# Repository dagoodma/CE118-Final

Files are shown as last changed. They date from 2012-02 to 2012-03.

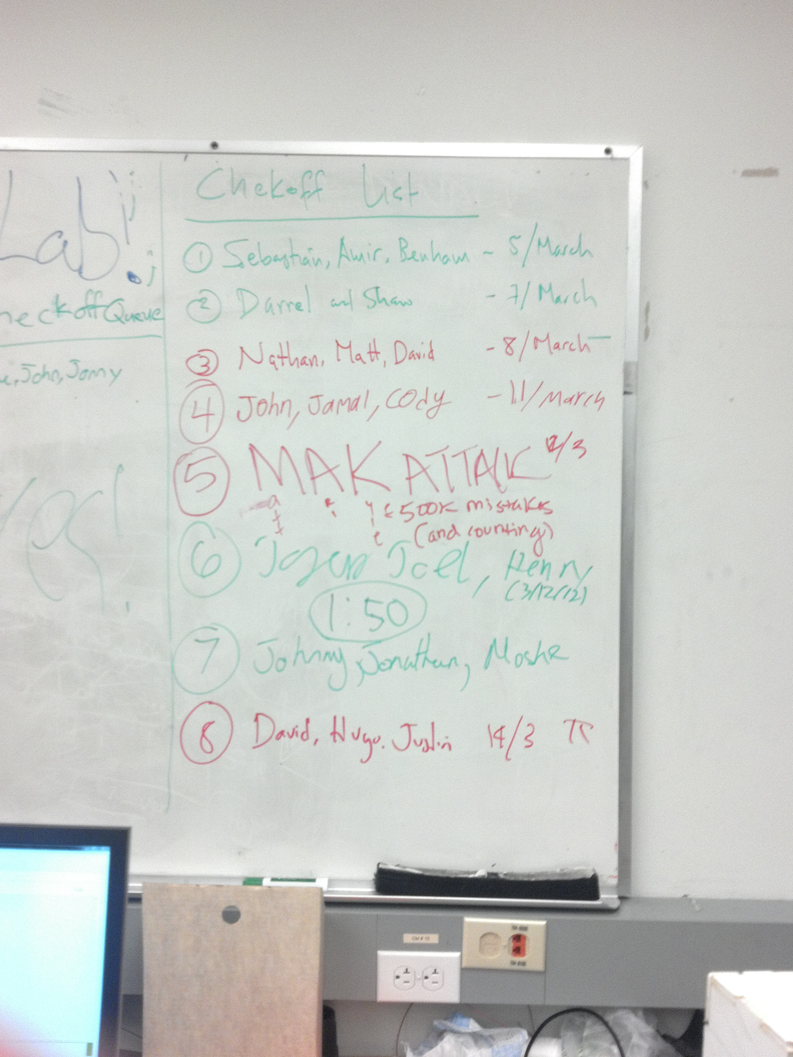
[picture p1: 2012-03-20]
Final Report/Pictures/Justin/checkoff board.jpg

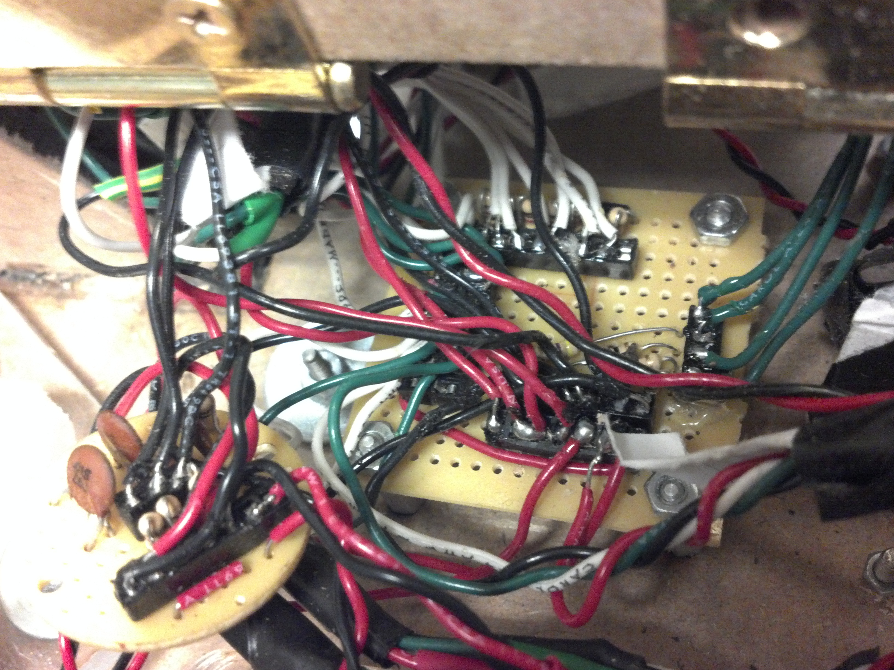
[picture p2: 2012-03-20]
Final Report/Pictures/Justin/bumper + tape board 2.jpg

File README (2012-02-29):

           . . . .... ......... ................            
              .  ...   .8DOOOOOOOD...............           
         .       . . .8OOOOOOOOOMNOOM,..........   M=7M     
  ....?  ............MOOOOOOOONNZOOOZN. ..  . ...~8  . ..  .
    N...,N .........8OOOOOOOOMM:.... O  .   .  .?, ONMM.    
  .,.,....=8........NOOOOOOID.  . .  : .     .OO.$  I. .    
  8...~:$ ... M7 ...OOOOD .M........ ......M:.: .   .M: .  .
...:..$.... .....,M.OOD..MMM : OMMM...,.M:......DM..........
....MMM,.. ,M8.....MMMMMMMMM..~MMMMM. 7 ....$N  ............
... ............7M8~$ DMMMMM.M MMMMM.. . N+.................
... .............. .M..OMMD MMZ ., M.:88 ...................
. .   ............N+ZO. ...,MMM ....MD......................
  .   .............N..++M...+  ...M M.......................
... ...............OOMZ.?........ ..  MN....................
... ............8Z7DO8O..+8::7:?+8.., ...,M~ ...............
......      :M?...8DOO8=..IMMMMM:..M .:M~....8M ....,O......
.....DMMNI .8 ..M,OOMO8O... ,=.8........ .M......=$....$....
....D7~?M7 ..=M...OODONNO.........8 ....... 7 ...DN , ,.....
...:... 7,.8:.....NOMOMOO=~......O............M...,~..O.....
...M..Z  .+ ......+OOONOM..MZNMM...............I ..::D .....
... ,..D Z    .  ..MONOOZ........................O ,O ......
....MM= 8.. .......$N.8OM.........................  ........
... ..     ...........8OZ...................................
......      ..........DM....................................
.......... .................................................

Future TODO:
----------------
* State machine and Code for tapesensors 
* Add pin names into schematics

Febuary 28, 2012
----------------
* Ready to print out of MDF
* Determine beacon switching with ULN2003A
    - update schematic
* Test gate servo
    - write code
* Prototype and test drive motor servo
* 

Febuary 21, 2012
----------------
* Prototyped geneva wheel: works.
* Started code.

/-----------------------------------------------------------\
--------------- How to use git -------------------
##Checkout from Github:
    git clone git@github.com:dagoodma/CE118-Lab

To commit code to the github first be sure your SSH public key is
generated in .ssh and added to your github account.

## See the changes files
    git status -s

## Add changed files
    git add -A

## Commit to local repository
    git commit -a -m "Your message"

## Commit to github (be sure to see http://help.github.com/create-a-repo/)
    git push -u origin master

-------- How to configure ssh public key  ------------

Once you have a github account you must configure your public ssh key
for each computer you wish to use.

## Generate an ssh-rsa public key
    ssh-keygen

Next, copy the contents of id_rsa.pub and login to your github account.
Under account settings > SSH Keys click Add New SSH Key, paste, and 
done.

## Configure info
    
    git config --global user.name "Your Name"
    git config --global user.email your@email.com

--------------- Add a repository -------------------

Next steps:
  mkdir CE118-Lab3
  cd CE118-Lab3
  git init
  touch README
  git add README
  git commit -m 'first commit'
  git remote add origin git@github.com:dagoodma/CE118-Lab3.git
  git push -u origin master
      
Existing Git Repo?
  cd existing_git_repo
  git remote add origin git@github.com:dagoodma/CE118-Lab3.git
  git push -u origin master

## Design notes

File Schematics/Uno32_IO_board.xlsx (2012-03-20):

CMPE118 Uno32 I/O Board Connection Table:
PIC32 Pin # | Connector Pin # | chipKIT Pin # | PIC32 Signal | Protection Pin # | Notes
15 | J5-16 | 41 | PGC1/AN1/VREF-/CVREF-/CN3/RB1 | Battery Voltage | Inaccesible from I/O
14 | J7-01 | A00/14 | C2IN-/AN2/SS1/CN4/RB2 | PORTV-3 | RC Servo | ADC
13 | J7-02 | A06/20 | C2IN+/AN3/CN5/RB3 | PORTV-4 | Gate (RC Servo) | ADC |  | RC Servo
12 | J7-03 | A01/15 | C1IN-/AN4/CN6/RB4 | PORTV-5 | TAPE_LEFT | ADC |  | Perfboard
11 | J7-03 | A07/21 | C1IN+/AN5/CN7/RB5 | PORTV-6 | TAPE_CENTER | ADC |  | Perfboard
21 | J7-05 | A02/16 | U2CTS/C1OUT/AN8/RB8 | PORTV-7 | TAPE_RIGHT | ADC |  | Perfboard
22 | J7-06 | A08/22 | PMA7/C2OUT/AN9/RB9 | PORTV-8 | TAPE_BACK | ADC |  | Perfboard
24 | J7-08 | A09/23 | TDO/PMA12/AN11/RB11 | PORTW-3 | TAPE_ARMFRONT | ADC |  | Perfboard
23 | J7-07 | A03/17 | TMS/CVREFOUT/PMA13/AN10/RB10 | PORTW-4 | TAPE_ARMLEFT | ADC |  | Perfboard
28 | J7-10 | A10/24 | TDI/PMA10/AN13/RB13 | PORTW-5 | TAPE_ARMRIGHT | ADC |  | Perfboard
27 | J7-09 | A04/18 | TCK/PMA11/AN12/RB12 | PORTW-6 | IR Main (RC Servo) | ADC |  | IR
30 | J7-12 | A11/25 | PMALL/PMA0/AN15/OCFB/CN12/RB15 | PORTW-7 | IR Angle (RC Servo) | ADC |  | IR
29 | J7-11 | A05/19 | PMALH/PMA1/U2RTS/AN14/RB14 | PORTW-8 | RC Servo | ADC
32 | J5-14 | 40 | PMA8/U2TX/SCL2/CN18/RF5 | PORTX-03 | LED_BANK3_2, RC | I/O
16 | J5-15 | 42 | PGED1/PMA6/AN0/VREF+/CVREF+/CN2/RB0 | PORTX-04 | LED_BANK3_3, RC | I/O
4 | J5-11 | 13 | SCK2/PMA5/CN8/RG6 | PORTX-05 | LED_BANK3_0 | I/O
31 | J5-12 | 39 | PMA9/U2RX/SDA2/CN17/RF4 | PORTX-06 | LED_BANK3_1 | I/O
5 | J5-09 or J5-07 | 12 | SDI2/PMA5/CN8/RG7 | PORTX-07/9 | LED_BANK2_2*, DNU | I/O
35 | J5-10 | 38 | U1RTS/BCLK1/SCK1/INT0/RF6 | PORTX-08 | TAPE_LEDS2 (LED_BANK2_3) | I/O | J2-9 (D) | ULN
6 | J5-07 or J5-09 | 11 | SDO2/PMA3/CN10/RG8 | PORTX-09/7 | LED_BANK2_0*, DNU | I/O
55 | J5-08 | 37 | CN16/RD7 | PORTX-10 | LED_BANK2_1 | I/O
52 | J5-05 | 10 | PMWR/OC5/IC5/CN13/RD4 | PORTX-11 | PWM5 | I/O
54 | J5-06 | 36 | CN15/RD6 | PORTX-12 | LED_BANK1_3 | I/O
45 | J5-04 | 35 | IC4/PMCS1/PMA14/INT4/RD11 | PORTY-03 | LED_BANK1_2 | I/O
51 | J5-03 | 9 | OC4/RD3 | PORTY-04 | PWM4, LED_BANK1_1 | I/O
53 | J5-02 | 34 | PMRD/CN14/RD5 | PORTY-05 | LED_BANK1_0 | I/O
44 | J5-01 | 8 | IC3/PMCS2/PMA15/INT3/RD10 | PORTY-06 | RC Servo | I/O
3 | J6-16 | 33 | PMD7/RE7 | PORTY-07 | RC Servo | I/O
43 | J6-15 | 7 | IC2/U1CTS/INT2/RD9 | PORTY-08 | TAPE_LEDS1 | I/O | J2-11 (F) | ULN
2 | J6-14 | 32 | PMD6/RE6 | PORTY-09 | Hbridge Dir A | I/O | J1-11 | Hbridge
50 | J6-13 | 6 | OC3/RD2 | PORTY-10 | Hbridge Step A (PWM3) | I/O | J1-12 | Hbridge
1 | J6-12 | 31 | PMD5/RE5 | PORTY-11 | Hbrige Dir B | I/O | J1-7 | Hbridge
49 | J6-11 | 5 | OC2/RD1 | PORTY-12 | Hbridge Step B (PWM6) | I/O | J1-8 | Hbridge
64 | J6-10 | 30 | PMD4/RE4 | PORTZ-03 | BUMPER_BR | I/O |  | Perfboard2
59 | J6-09 | 4 | RF1 | PORTZ-04 | BUMPER_BL | I/O |  | Perfboard2
63 | J6-08 | 29 | PMD3/RE3 | PORTZ-05 | BUMPER_BF | I/O |  | Perfboard2
46 | J6-07 | 3 | OC1/RD0 | PORTZ-06 | PWM1 | I/O
62 | J6-06 | 28 | PMD2/RE2 | PORTZ-07 | TAPE_LED | I/O | J2-12 (G) | ULN
42 | J6-05 | 2 | IC1/RTCC/INT1/RD8 | PORTZ-08 | RC Servo | I/O
61 | J6-04 | 27 | PMD1/RE1 | PORTZ-09 | RC Servo | I/O
33 | J6-03 | 1 | U1TX/SDO1/RF3 | PORTZ-10 | DO NOT USE | I/O
60 | J6-02 | 26 | PMD0/RE0 | PORTZ-11 | TAPE_LEDS3 | I/O | J2-10 (E) | ULN
34 | J6-01 | 0 | U1RX/SDI1/RF2 | PORTZ-12 | DO NOT USE | I/O

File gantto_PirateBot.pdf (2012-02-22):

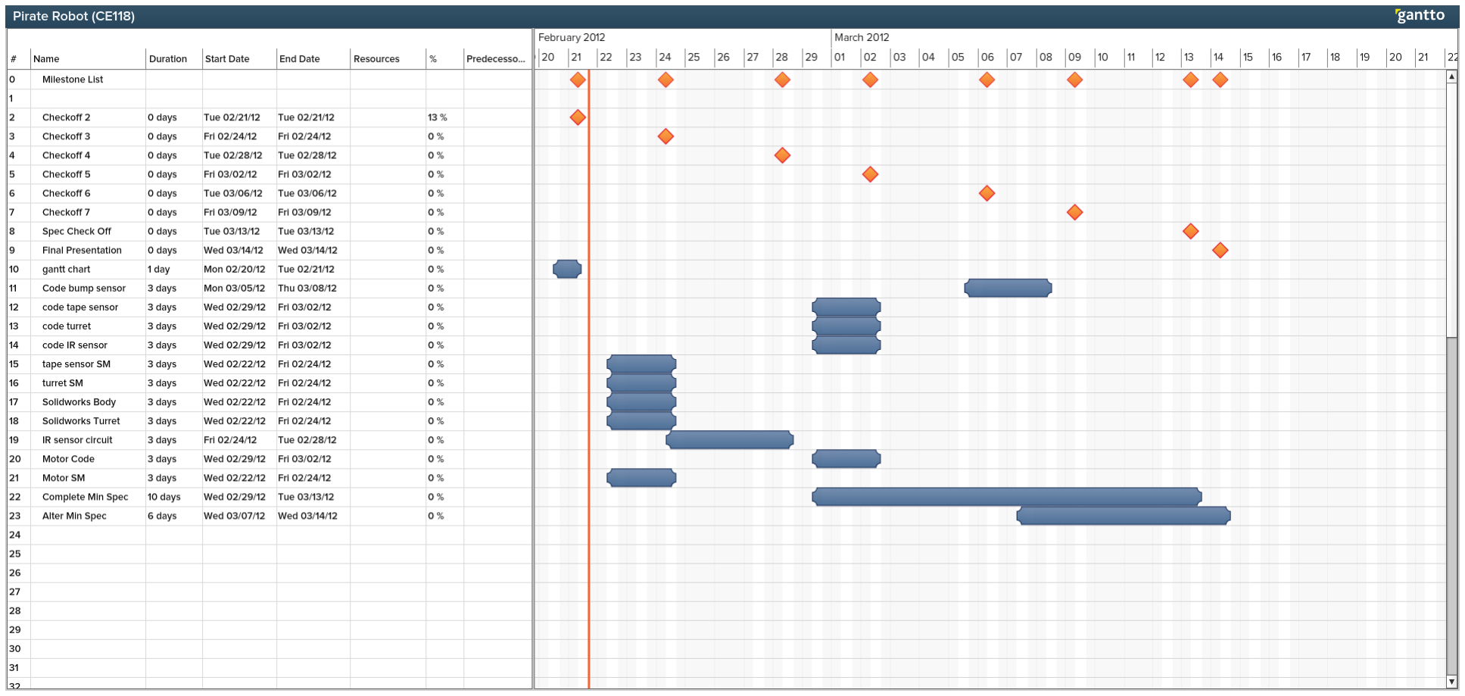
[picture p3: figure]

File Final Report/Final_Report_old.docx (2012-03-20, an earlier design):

Slugs of the Caribbean - Autonomous Robot
UCSC, CE118 Final Project

Introduction

The Slugs of the Caribbean project consisted of designing, constructing, programming, and testing an autonomous robot to meet the minimum specifications for the CE118 final project:

  - Navigate to the opposing island and back within two minutes
  - Hit the opponent with at least two ping pong balls
  - Stay within the field demarcated by two inch thick black tape
  - Detect and resolve collisions with an immovable object
  - The robot must be fully autonomous and cannot be controlled remotely

The project was assigned and completed within a five week period, and proved to be very challenging and time consuming. It taught us many new skills that drew from a variety of disciplines including: mechanical, electrical and computer engineering. Our goal was to develop the simplest robot possible, and later improve its capabilities as much as the remaining time allowed. Not everything worked out exactly as we had planned, but the end result successfully completed the minimum specification trial run with fifteen seconds to spare.

Designing and Planning

The three of us began the project by contributing five unique designs each, for a total of fifteen designs. The final design we chose to pursue was a combination of each of our best ones. However, we simplified the ping pong ball launcher into a box with a hinged gate that sprung open when released by an RC servo. Originally, we were designing a modular solution that would allow us to swap out the box for a rotating turret if we had the time to do so, which was not the case.

Both designs can be viewed below in figure 1.

<Minspec and turret schematics from first week>

A good portion of our time was spent in SolidWorks creating a comprehensive CAD model of our robot. Although we prototyped our design with foamcore, the final product was cut from MDF, and joined together using the tab and slot method. The CAD design of our robot is attached and can be seen in appendix A. A good amount of research and planning went into the actuators and sensors on our robot.

Drive motors

In order to make the robot mobile we purchased two 12 V, 140 RPM gearhead DC motors, which were screwed in and fixed to the body platform by motor mounts that we designed. These mounts consisted of a thin acrylic faceplate and MDF top and sidewalls. The motor shafts were attached to two wheels, which were made from thick acrylic, while the back and front of the robot was supported by skid plates created from ¼” thick bolts.

Collision sensors

Our durable collision sensors (bumpers) were made from thick acrylic plates that we cut and bent at ninety degree angles. The flat bumper plates were attached to the bent pieces with machine screws and nuts, and tension was maintained by short springs. Small push buttons were attached behind the bumpers to allow our robot to detect collisions.

Gate release

We used a servo motor as a gate release. When the servo was at the neutral position the gate would remain closed. Two springs were mounted behind the gate, and when the servo head was sent to the -45° position the gate was free to spring open. A motor mount was made for the servo out of MDF and attached just behind the gate.

Infrared Sensors

The infrared sensors that we designed and soldered in lab 2 proved to be robust enough to use on our final robot. We experimented with switching between two photodiodes on one circuit we elected to use two separate circuits detecting signals from two photodiodes oriented at an angle to allow for both long and short range detection. Each circuit was modified slightly to take an output from the peak detector allowing for software hysteresis. Both photodiodes were placed in MDF shielding to block light entering from the sides and give good directionality to our main beacon.

Tape Sensors

We used 7 of the TCRT5000 tape sensors provided in our lab kit for navigation of the course. Our arrangement allowed for high resolution coast following on the right side as well as detection of corners and the enemy base, with one sensor in the back to prevent reversing onto land. The ULN2003A board provided to us proved invaluable for simplification in driving our tape sensors, allowing for all 7 sensors to be switched easily using 3 ports on the PIC32. A perfboard with all our inputs and outputs as well as power and loading resistors for each LED/PD on the tape sensor had to be carefully soldered (twice) in order for our sensors to work properly.

Once a majority of the design work was completed we began by testing our design and creating prototypes of the actuator and sensor elements individually.

Prototyping and Modeling

To prototype our actuators and sensors we used foamcore instead of the more expensive MDF. Aside from prototyping the launcher and ‘geneva wheel’ loader for the turret design, which were never implemented, the first element we tested were our collision sensors.

us over the course of this project The microcontroller used by a PIC32MX320F128H donated by MicroChip.

…

The Tape Sensors

Our tape sensor implementation is fairly simple on its surface; however once we began to solder up all of the components its complexity became apparent. Each tape sensor has 4 leads, cathode and anode for the LED as well as collector and emitter for the photodiode. The LED anode and phototransistor cathode leads went into a board which provided 3.3V power from a TIP122 voltage regulator. Each LED needed a 150ohm loading resistor and was grounded with the ULN2003, capable of sinking current from two LEDs at each port. The photodiodes were placed in a sourcing configuration with a 1K resistor to ground with output was taken at the emitter using the ‘W’ analog port on the PIC32. The LEDs can be switched off and on by switching the ports on the ULN using the ‘Z’ ports and we then cascade through our analog inputs to take tape sensor readings.

As we soldered together our tape sensor board it quickly turned into a rats nest of wires leading into a small perfboard. 4 leads for each sensor * 7 sensors + 4 leads to the ULN meant we had 42 wires coming out of our perfboard, not to mention resistors and power regulation. This board was made even denser by the addition of bump sensor circuitry to the same perfboard. Despite the complexity our first assembled board worked reasonably well and we were able to use our sensors to design and implement our tape sensor code. Unfortunately with only a few days before min spec two of our tape sensors started to behave erratically, with no obvious software or hardware solution. After probing our tape sensor circuit for several hours we determined that there was no recourse but to resolder the whole board. Thankfully professor Elkaim was able to step in help us solder up the new board in record time.

The redone tape sensor board worked great, and all of our sensors gave readings close enough together that we did not have to deal with the additional complexity of separate thresholds for each sensor.

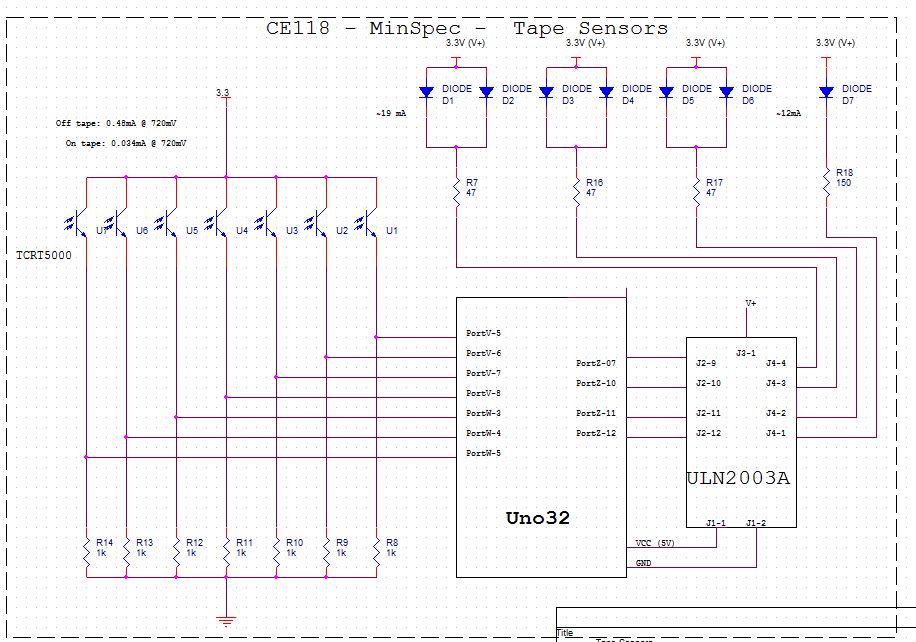
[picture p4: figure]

The software we used for the tape sensor made use of a simple state machine and a [synchronous?] sampling counter to ensure we had accurate readings at all times. Our state machine turned the leds on/off, took four readings, averaged them, repeated the process, and takes the difference of ‘ON’ and ‘OFF’ states to get a reading. High values correspond to being off tape, and low on tape. In practice we ended up taking only two samples during each state to speed up our sampling rate which in turn allowed us to navigate the course slightly faster. <insert state machine diagram?>

The Infrared Sensors

From very early on we wanted a two infrared sensor arrangement to allow for both long and short range detection of enemies, the idea being that we lock on with the main beacon and a second one placed at an angle notifies us when we are within range to dump / charge ahead over tape. Our original idea to save space on our bot and (in theory) reduce complexity was to switch two photodiodes on/off on the same circuit using a hex inverter. While we were able to implement a circuit that switched between two detectors on the same circuit we had nothing but trouble with interference between the two detectors. After working with the circuit trying to determine which capacitors weren’t discharging or where our initial voltage spikes were coming from we elected to cut our losses and place an additional sensing circuit on our board. While this detracted from the simplicity of our design it did not cost us any I/O ports and worked well with some minor alterations.

We first thought that we could get by with taking output from the comparator of the two circuits, saving us some software complexity, but quickly abandoned this idea in favor of a software comparator. The hardware comparator did not allow us much in the way of accuracy and our final navigation made use of a find max IR signal function which would not have been possible without taking output from our peak detectors. In order to get good resolution off our peak detector we had to alter it’s time constant for a faster discharge with a smaller resistor.

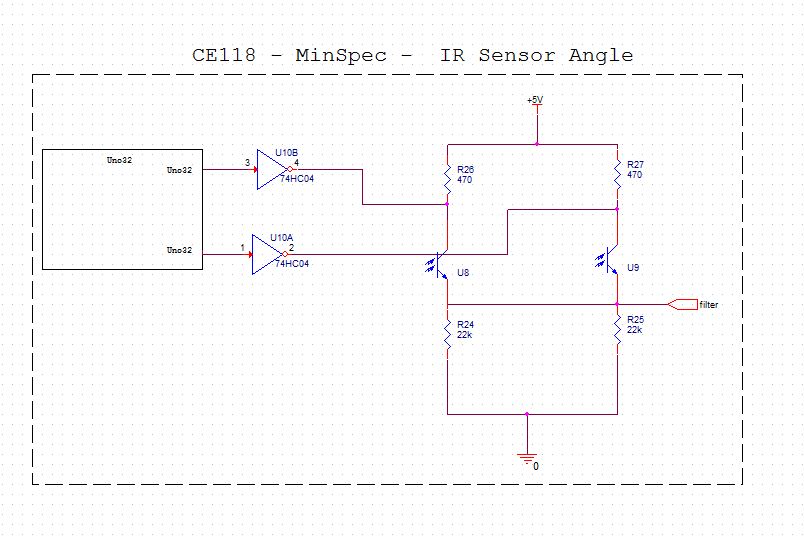
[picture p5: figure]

<switch schematic>

<David & Justin’s Schematics in appendix>

The Collision Sensors

In theory we wanted very robust bump sensors to allow us to ram into the other robots without sustaining any structural damage ourselves. In practice we ended up with some exquisitely designed bumpers that were perhaps somewhat overkill for our slow-moving robot.

Our durable collision sensors (bumpers) were made from thick acrylic plates that we cut and bent at ninety degree angles. The flat bumper plates were attached to the bent pieces with machine screws and nuts, and tension was maintained by short springs. Small push buttons were attached behind the bumpers to allow our robot to detect collisions.

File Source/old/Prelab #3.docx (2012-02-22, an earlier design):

Hugo A. Hernandez

David Goodman

Pre-Lab #3

0.1) Ports and pins to output to the motors in each part:

To drive the motor we will be using the following ports and pins on the: HBridge DRV8814, jumper stack J2 pins 1 and 2; DRV8811, jumper stack J2 pins 1 and 2; D53658, jumper stack J1 pin 1.

0.2) Initializations required:

Port Z pins 3,4,6,7,8 should be configured as outputs, and port V pin 5 as an input. The PORTS_SetPortDirection() function will be used to do this. Also, the A/D converter must be initialized with AD_Init(), the timer must be initialized with TIMERS_Init(), the RC Servo must be initialized with RC_Init(), the stepper motor will be initialized with Stepper_Init(), and the PWM must be initialized with PWM_Init();

0.3) ADC operating modes being used:

ADC_MODULE_ON Turn on ADC

ADC_FORMAT_INTG Output 16 bit unsigned int

ADC_CLK_AUTO Auto convert with internal counter

ADC_AUTO_SAMPLING_ON Auto sample

ADC_VREF_AVDD_AVSS Internal + and – voltage references configured

ADC_SCAN_ON ADC scan selection for CHO

ADC_BUF_16 16-bit word buffer

ADC_SAMPLE_TIME_31 31 Tad auto sample time

ADC_CONV_CLK_32Tcy A/D conversion clock select bit

ADC_CONV_CLK_PB A/D conversion clock from PB clock

0.4) Device connections:

Uno32 Connections

UNO Port-Pin | Device | Device Port-Pin | Comments
Z-03 | DRV8814 | J1-11 | Direction A
Z-04 | DRV8814 | J1-12 | Enable A
Z-07 | DRV8814 | J1-7 | Direction B
Z-08 | DRV8814 | J1-8 | Enable B
Z-03 | DRV8811 | J5-4 | Direction
Z-04 | DRV8811 | J5-5 | Enable
Z-06 | DRV8811 | J5-3 | PWM -> step
Z-06 | DS3658 | J2-9 | PWM -> Ch.A
V-05 | 50k pot | Middle Pin (Wiper) | (Input)

DRV8814 Connections

DRV8814 Port-Pin | Purpose | Comments
J1 | Inputs | See Uno32 Connections
J2-1 | Motor power
J2-2 | Motor ground
J3-1 | Power (8 – 30V)
J3-2 | High current ground
J6-open | Brake | Decay Mode
J6-closed | Coast | Decay Mode

DRV8811 Connections

DRV8811 Port-Pin | Purpose | Comment
J2-1 | Motor power
J2-2 | Motor ground
J5 | Inputs | See Uno32 Connections
J4|J3-00 | Full-Step | Coils Energized (2)
J4|J3-01 | Half-Step | Coils Energized (1-2)
J4|J3-01 | Quarter-Step | Coils Energized
J4|J3-11 | Eighth-Step | Coils Energized

DS3658 Connections

DS3658 Port-Pin | Purpose | Comment
J2 | Inputs | See Uno32 Connections
J1-1 | Motor power
J1-2 | Motor ground
J4-1 | +12V Supply
J4-2 | Ground
J3-open | Diodes unconnected | Kickback Diodes
J3-closed | Diodes to VCC | Kickback Diodes

0.5) Ribbon connector and the ports we will use are listed below:

Uno32 Port Z

1 | 3 | 5 | 7 | 9 | 11 | 13
| DirA/Step | En | DirB
| EnA/Dir | PWM-> Ch.A | EnB
2 | 4 | 6 | 8 | 10 | 12 | 14

DS3658

1 | 3 | 5 | 7 | 9 | 11 | 13
| | | | Ch. A
2 | 4 | 6 | 8 | 10 | 12 | 14
| | | DRV8814
1 | 3 | 5 | 7 | 9 | 11 | 13
| DirA | | DirB | | ?
| EnA | | EnB | | ?
2 | 4 | 6 | 8 | 10 | 12 | 14
| | | DRV8811
1 | 3 | 5 | 7 | 9 | 11 | 13
| Step | En
| Dir
2 | 4 | 6 | 8 | 10 | 12 | 14

0.6) PWM state diagram and an expected plot of its output at 10 kHz:

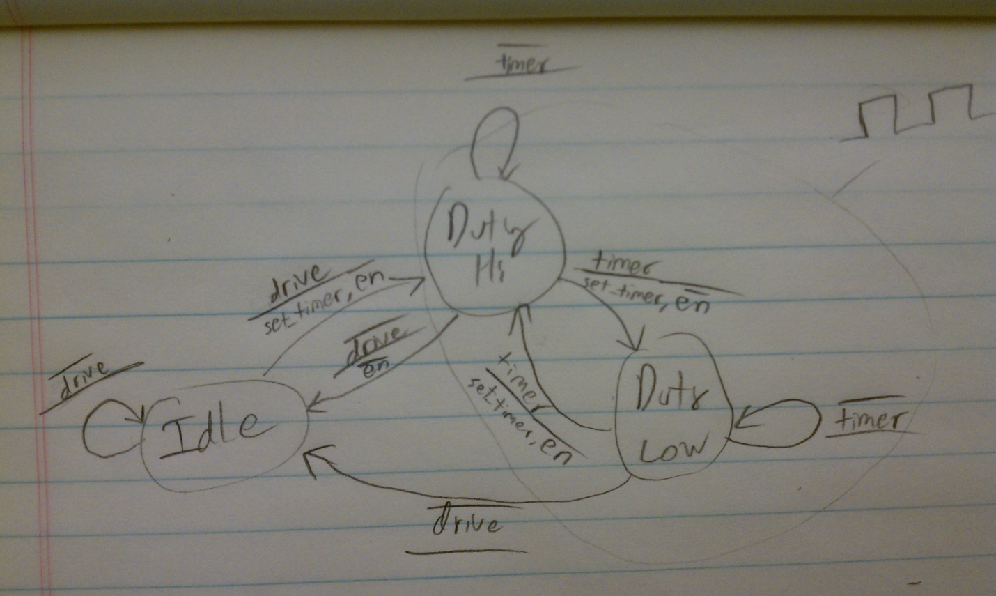
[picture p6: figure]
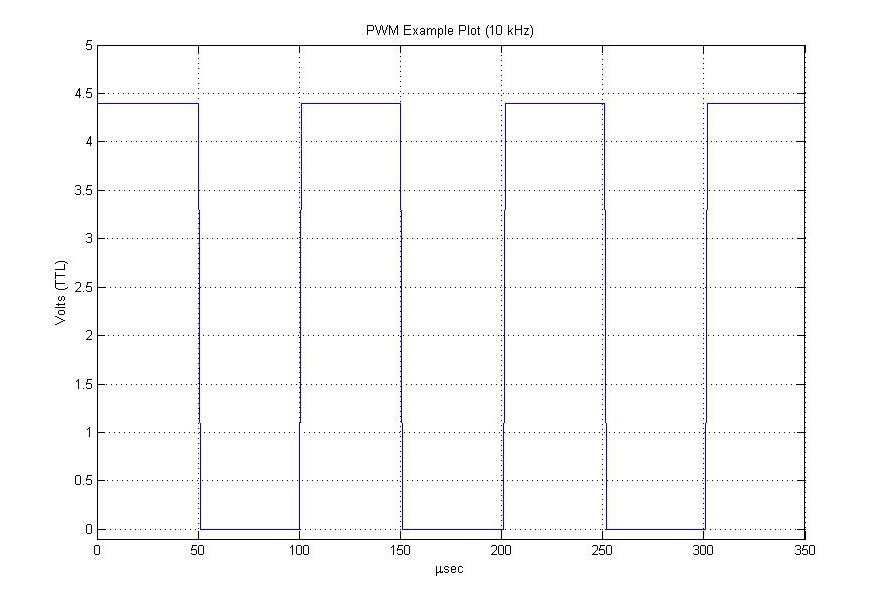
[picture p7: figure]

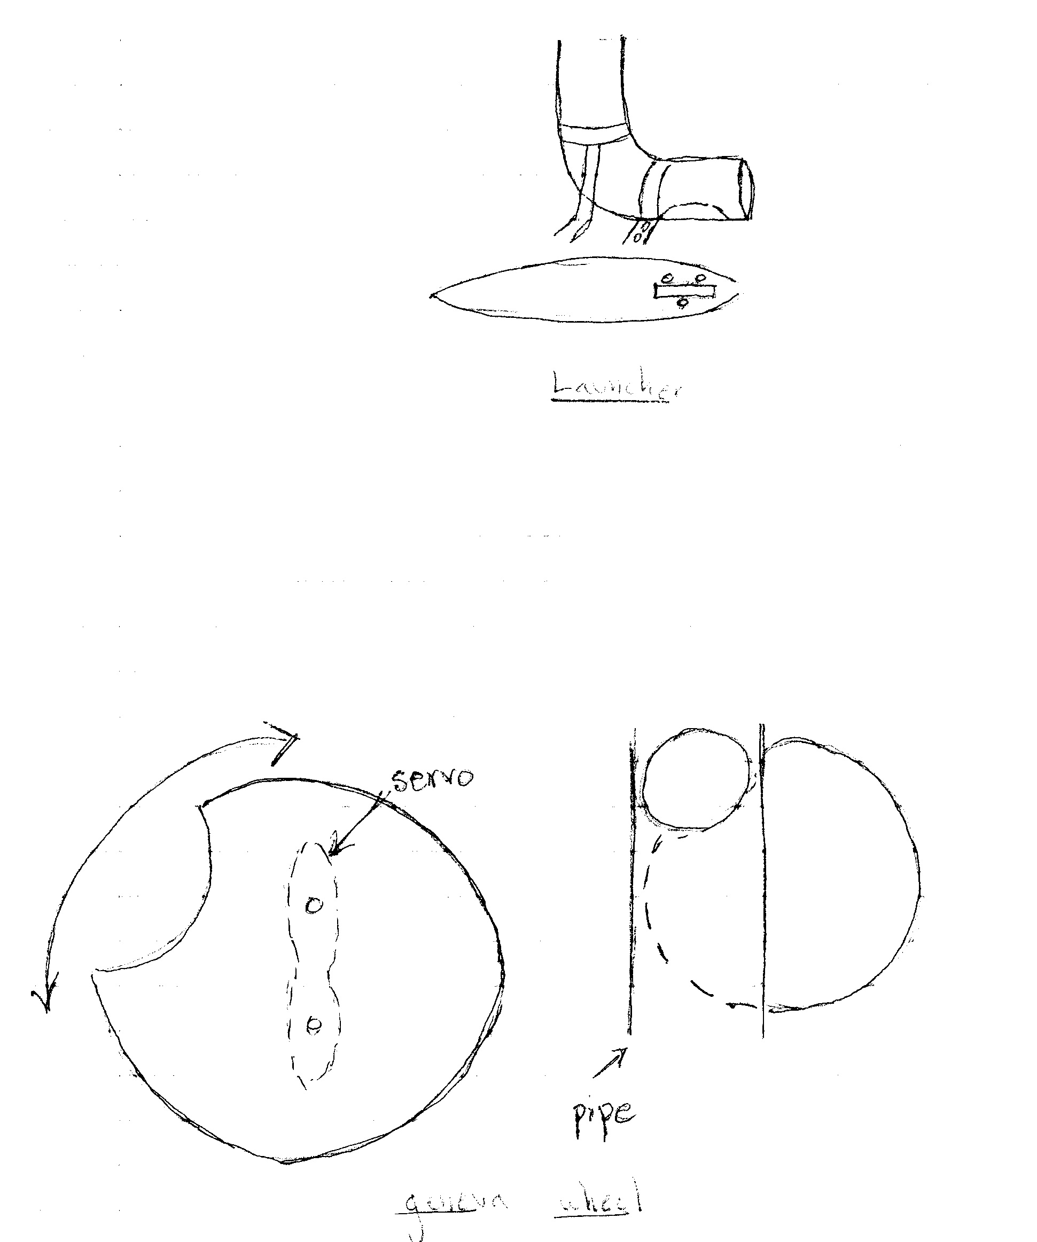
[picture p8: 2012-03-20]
Final Report/Pictures/Geneva Wheel.jpg

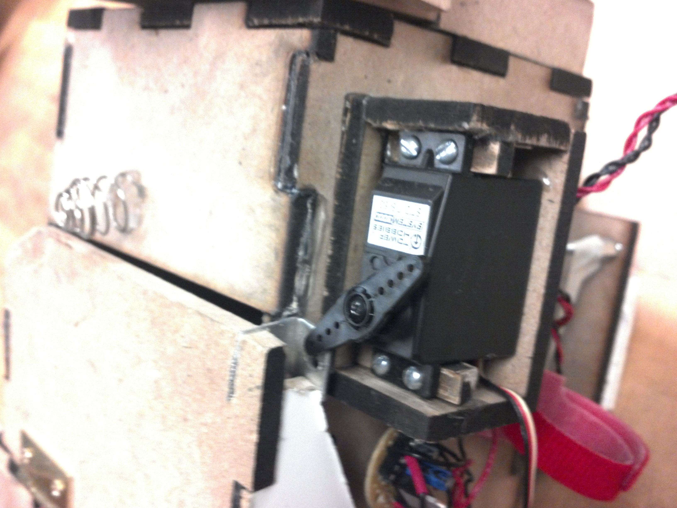
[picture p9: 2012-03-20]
Final Report/Pictures/Justin/servo gate.jpg

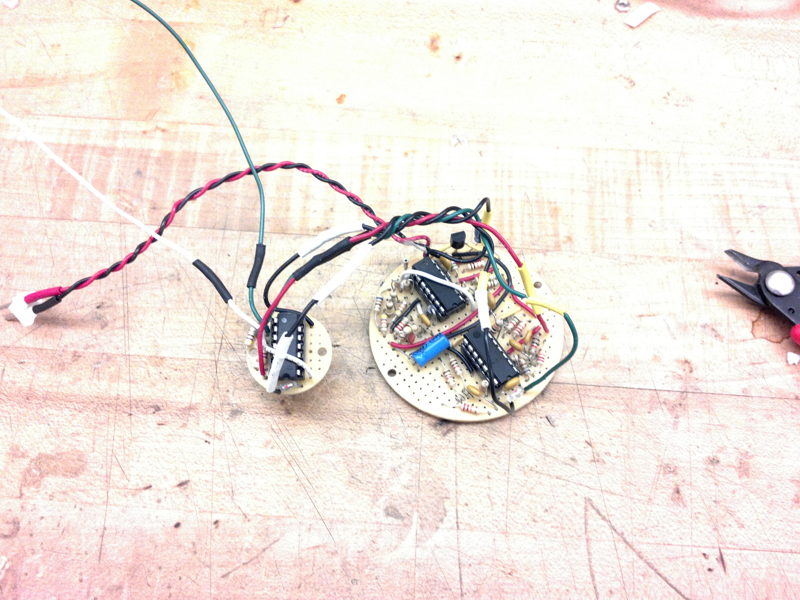
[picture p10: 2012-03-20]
Final Report/Pictures/Justin/IR + reg top.jpg

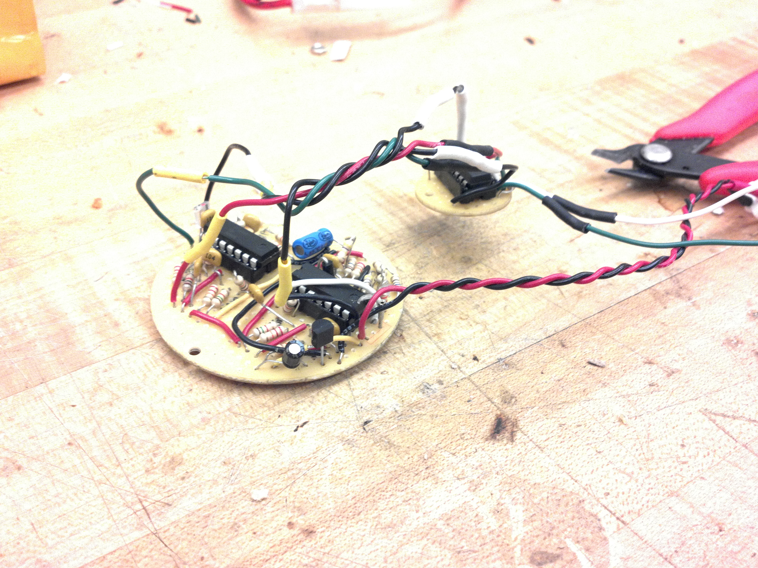
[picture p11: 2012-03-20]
Final Report/Pictures/Justin/IR + reg 2.jpg

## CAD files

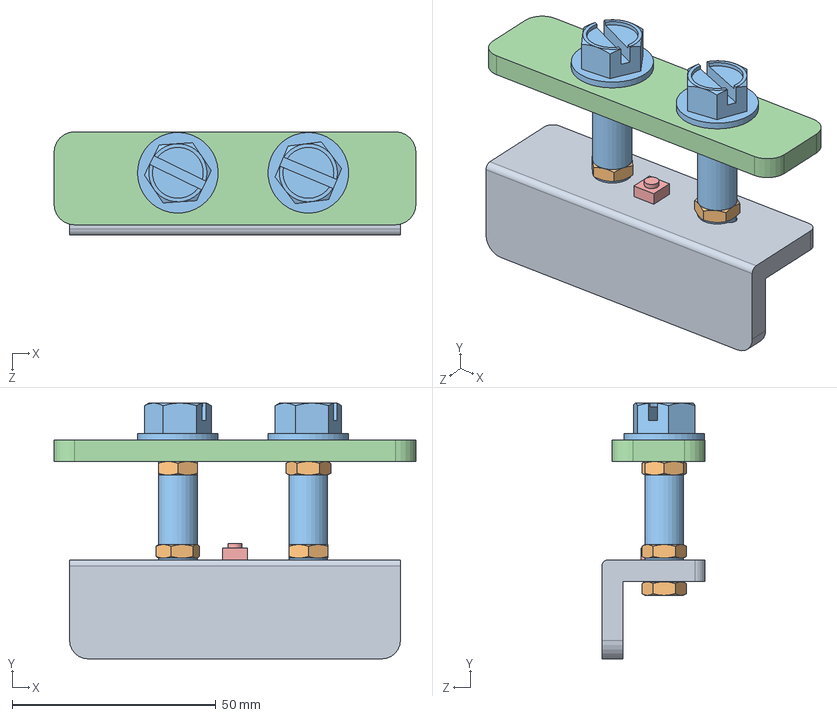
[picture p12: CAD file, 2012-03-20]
Solidworks/Bumper/Bumper_short.SLDASM
88.9 x 62.8 x 25.4 mm
bumperMount
machine screw nut hex_ai x 6
hex washer screw_ai x 2
bumperPlate_short
Button

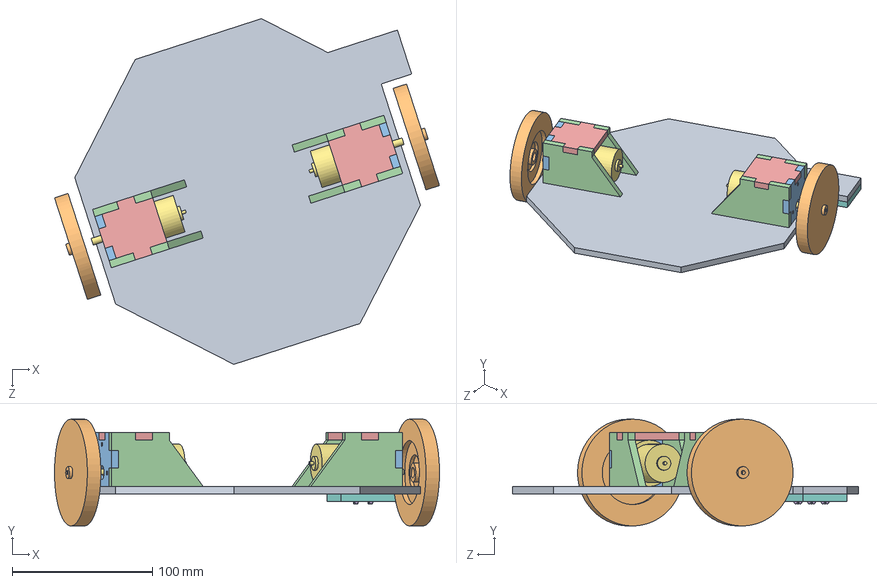
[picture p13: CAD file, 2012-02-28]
Solidworks/Platform.SLDASM
274.7 x 76.2 x 246.6 mm
base
Wheel x 2
motorMountFront x 2
motorMountSide x 4
motorMountTop x 2
tapeSensor_TCRT5000 x 3
12V65RPMGearheadMotor x 2
SideTapeSensorStand

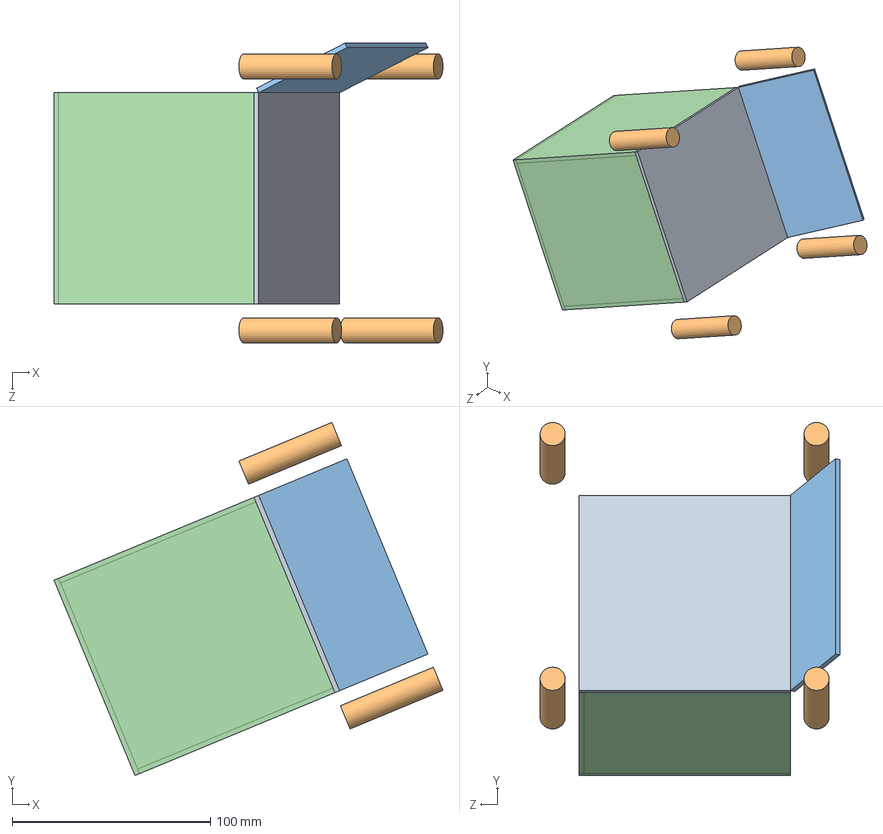
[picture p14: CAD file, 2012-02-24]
Solidworks/justin/PingPongBox.SLDASM
196.3 x 178.2 x 151.3 mm
BoxWall
BoxLeg x 4
HalfBoxWall x 2
boxWallWhole x 4

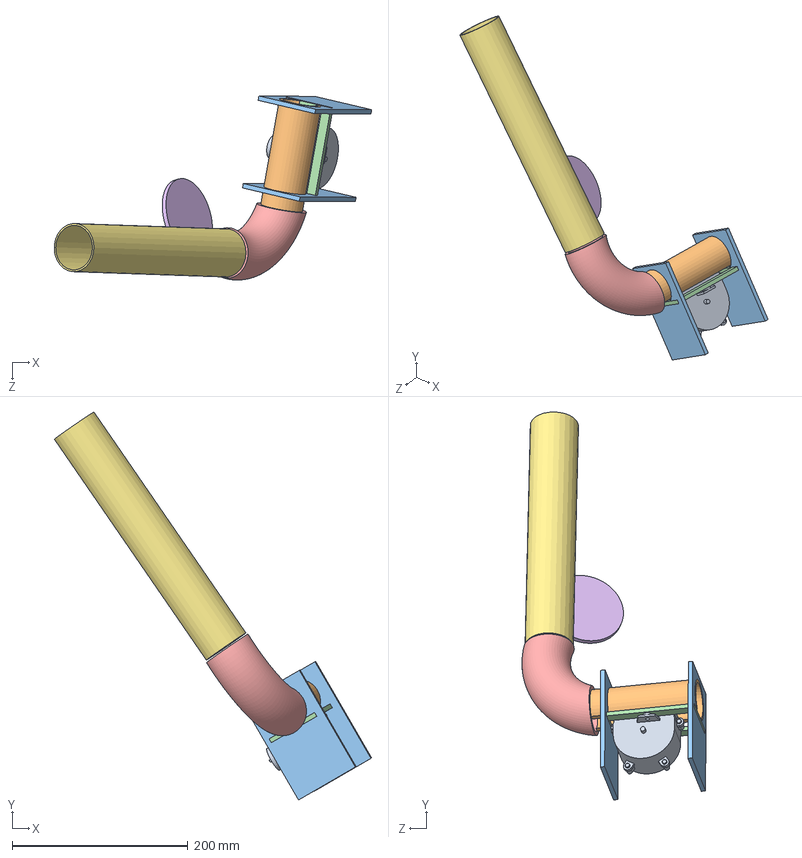
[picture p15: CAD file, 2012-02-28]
Solidworks/Launcher/Launcher with Mount.SLDASM
360.8 x 441.0 x 209.3 mm
ToyMotor
PVC_4.7in_cut
launch_side x 2
motor_mount
PVC_Elbow
genevaWheel
pvc
pingPongBall

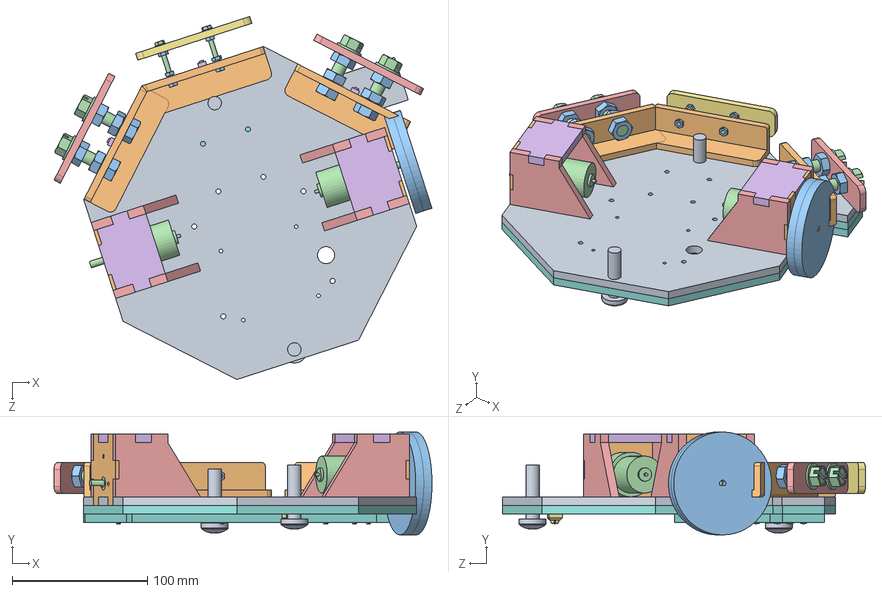
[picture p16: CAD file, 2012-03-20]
Solidworks/MinSpec/Platform.SLDASM
279.9 x 76.2 x 268.9 mm
base
mountFront2 x 2
wheelMDF x 2
12V65RPMGearheadMotor x 2
motorMountSide x 4
motorMountTop x 2
tapeSensor_TCRT5000 x 7
baseBottom
pan cross head_am x 2
bumperMount x 3
machine screw nut hex_ai x 18
hex washer screw_ai x 6
bumperPlate_short x 2
Button x 3
bumperPlate
tapePlatform

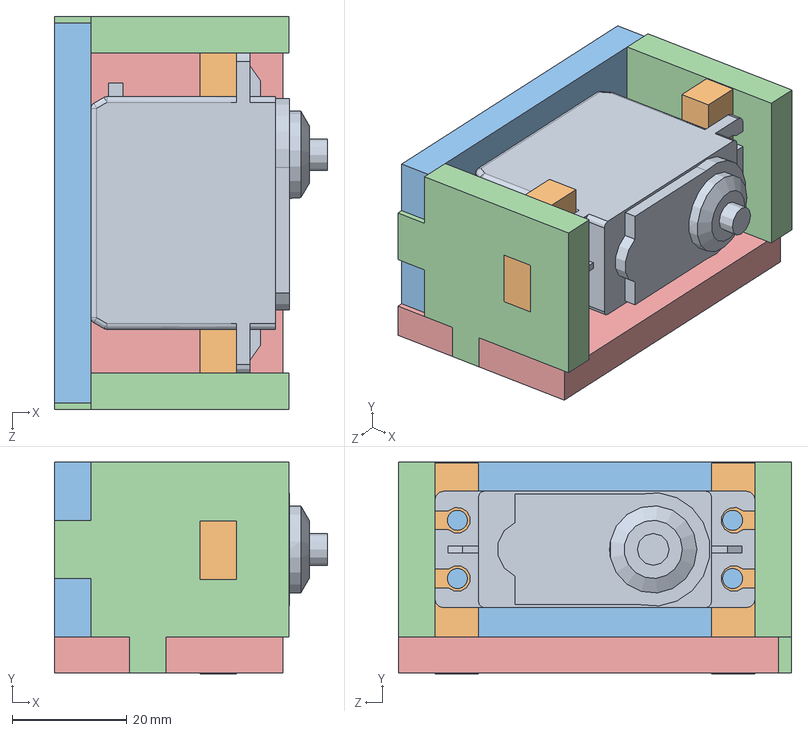
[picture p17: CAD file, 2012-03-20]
Solidworks/ServoBracket/ServoWithBracket.SLDASM
47.6 x 37.0 x 68.6 mm
servo
bracket_mount x 2
bracket_bottom
bracket_side2 x 2
bracket_back

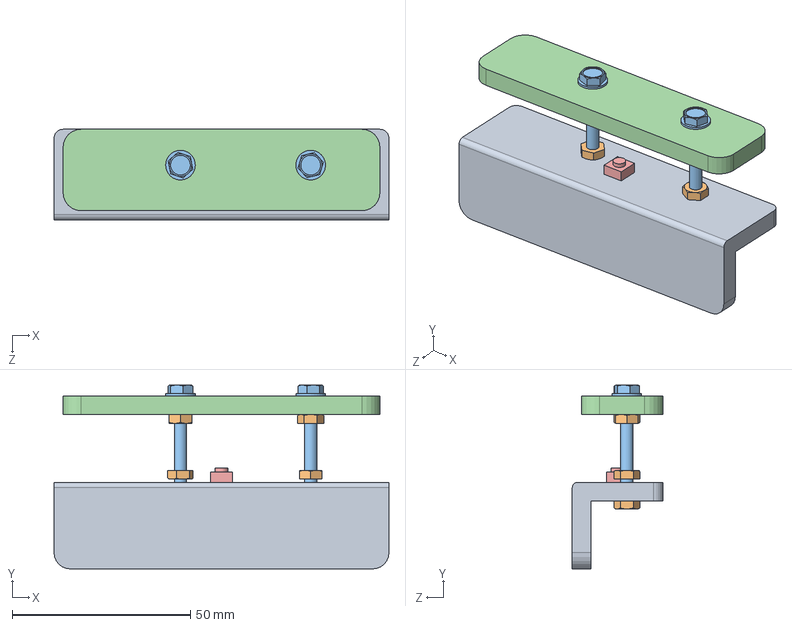
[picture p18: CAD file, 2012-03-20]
Solidworks/Bumper/Bumper.SLDASM
94.0 x 51.6 x 25.4 mm
bumperMount
machine screw nut hex_ai x 6
hex washer screw_ai x 2
bumperPlate
Button

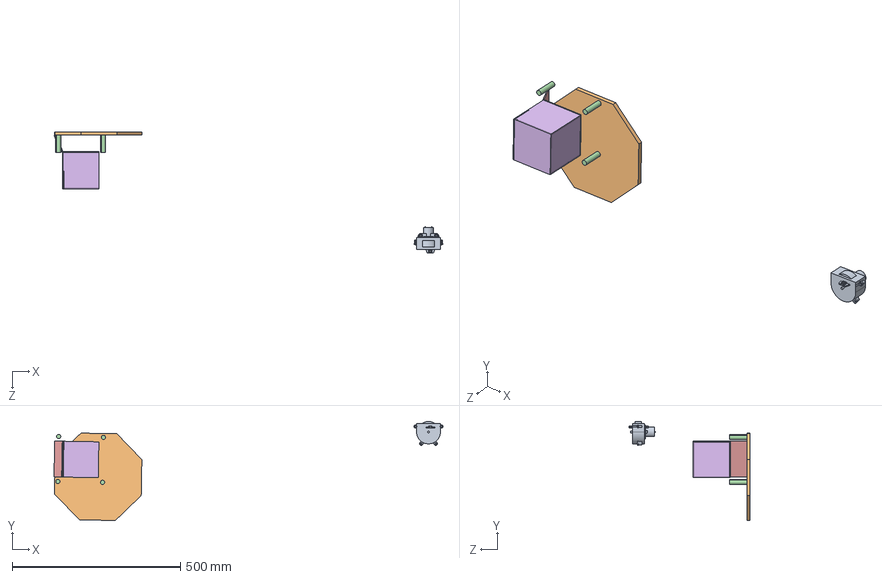
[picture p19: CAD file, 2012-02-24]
Solidworks/justin/FinalBot.SLDASM
1157.1 x 294.5 x 361.0 mm
ToyMotor
BotBody
BoxWall
BoxLeg x 4
HalfBoxWall x 2
boxWallWhole x 4

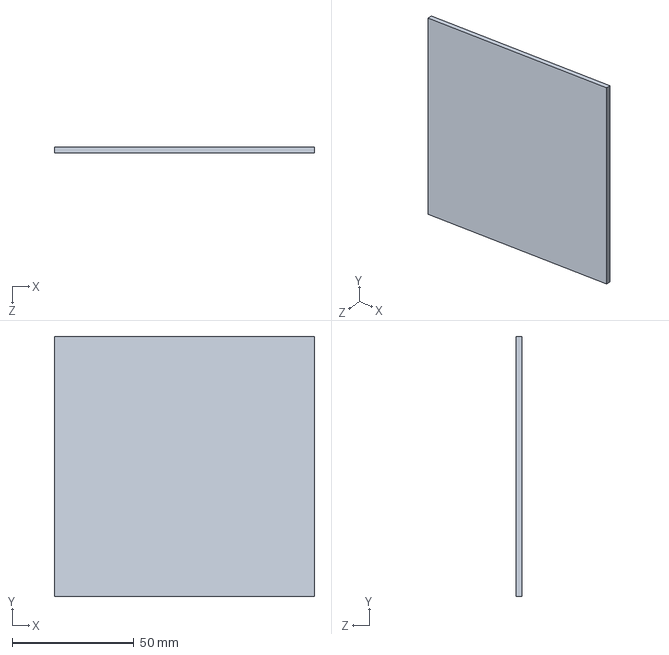
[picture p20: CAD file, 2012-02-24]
Solidworks/justin/boxWallWhole.SLDPRT
106.7 x 106.7 x 2.54 mm

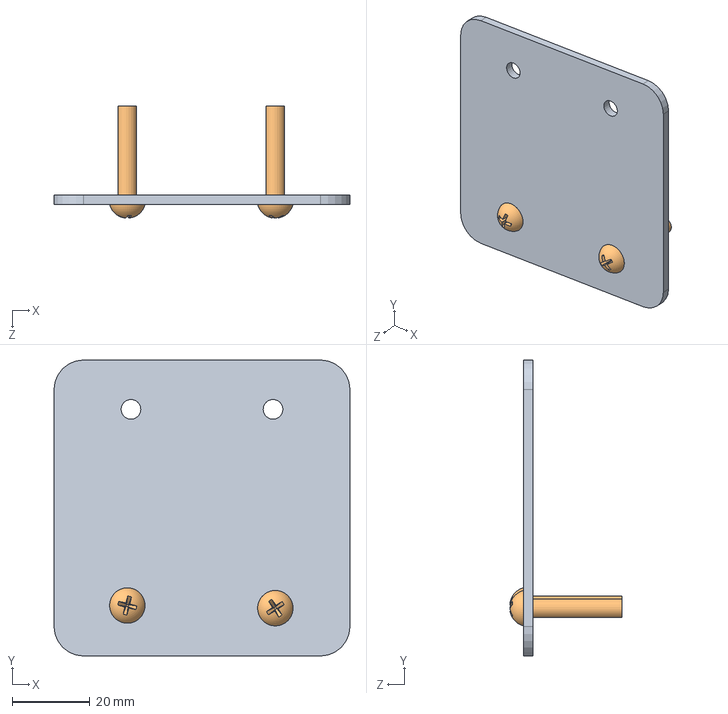
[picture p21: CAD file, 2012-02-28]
Solidworks/Bumper/lasercutter_bumer_base.SLDASM
76.2 x 76.2 x 28.8 mm
laser_cutter_acrylic_base
round head screw_ai x 2

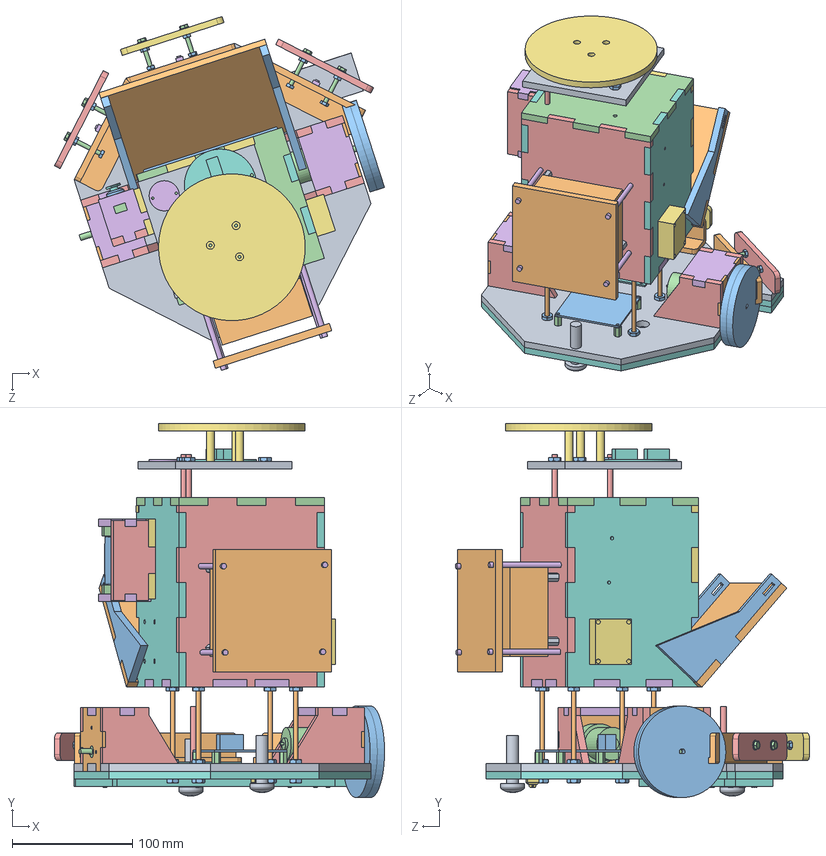
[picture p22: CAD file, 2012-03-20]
Solidworks/MinSpec/MinSpecRobot.SLDASM
274.3 x 310.9 x 294.1 mm
base
mountFront2 x 2
wheelMDF x 2
12V65RPMGearheadMotor x 2
motorMountSide x 4
motorMountTop x 2
tapeSensor_TCRT5000 x 8
baseBottom
pan cross head_am x 2
bumperMount x 3
machine screw nut hex_ai x 44
hex washer screw_ai x 6
bumperPlate_short x 2
Button x 3
bumperPlate
tapePlatform
pingPongBall
gate
gate_wall x 2
boxTop
boxBack
boxBottom
boxFront
boxSide x 2
standoffHex_uno32 x 4
uno32
hBridge_1_v2
standoffHex_hbridge x 4
Gate_Stop
beaconSensorSmall
beaconSensor
beaconPlatform
uno32ProtectorTop
servo
bracket_mount x 2
bracket_bottom
bracket_side2 x 2
bracket_back
servoHorn_2
truss head screw_ai x 4
boxBaseRod x 4
boxWedge_bottom
boxWedge_edge
beaconBoxRod x 2
ULN2003
bumperTapePerfBoard

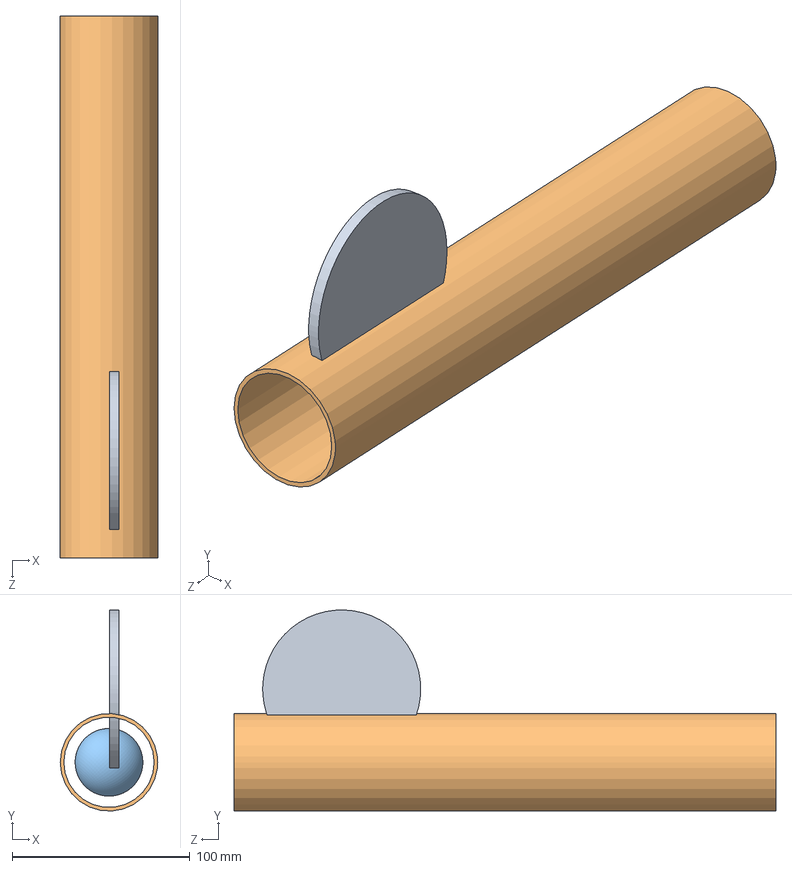
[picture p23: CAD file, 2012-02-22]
Solidworks/PitcherRelease.SLDASM
54.9 x 113.1 x 304.8 mm
genevaWheel
pvc
pingPongBall

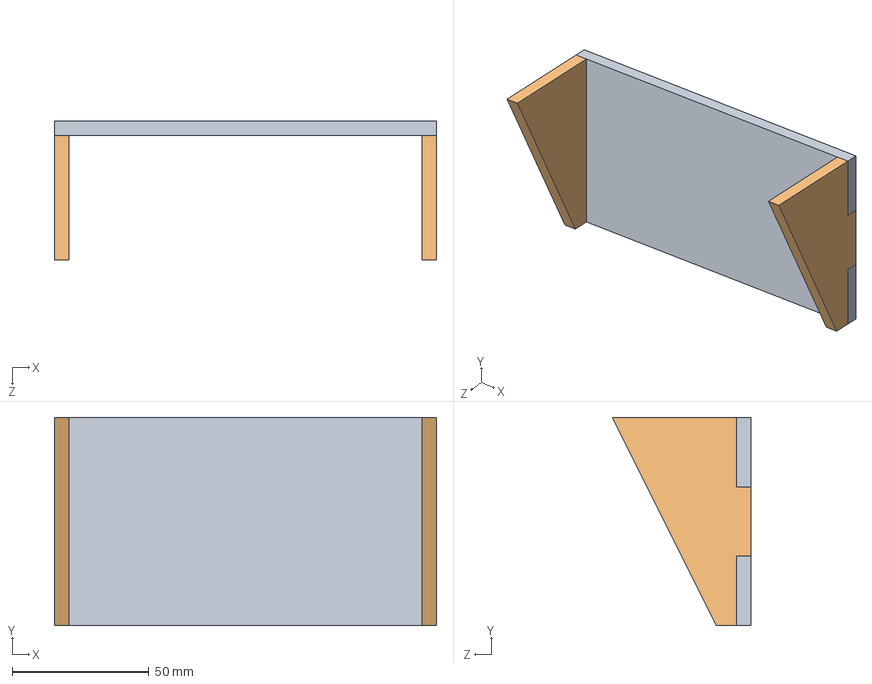
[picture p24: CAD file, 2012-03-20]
Solidworks/MinSpec/Gate.SLDASM
139.7 x 76.2 x 50.8 mm
gate
gate_wall x 2

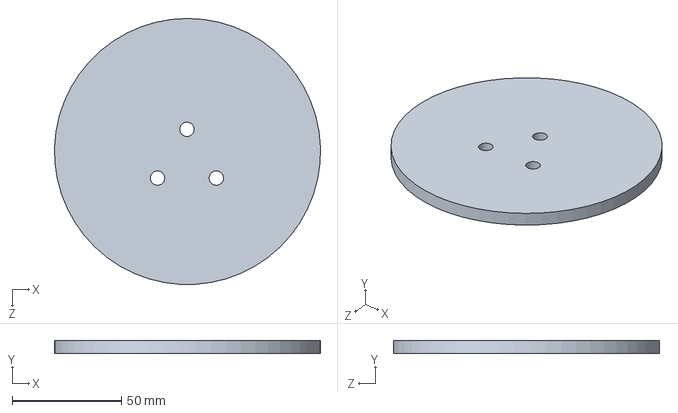
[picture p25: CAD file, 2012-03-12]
Solidworks/beacon.SLDPRT
121.9 x 6.10 x 121.9 mm

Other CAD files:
Solidworks/Bumper/lasercutter/Bumper_short.DXF
Solidworks/Drawings/tapePlatform.DXF
Solidworks/justin/boxFront.SLDPRT
Solidworks/Launcher/launcher_base.SLDPRT
Final Report/Solidworks Drawings/MinSpecRobot.SLDDRW
Final Report/Solidworks Drawings/base.SLDDRW
Solidworks/12V65RPMGearheadMotor.SLDPRT
Solidworks/Bumper/Button.SLDPRT
Solidworks/Bumper/bumperMount.SLDPRT
Solidworks/Bumper/bumperMount_LASER.SLDPRT
Solidworks/Bumper/bumperMount_short.SLDPRT
Solidworks/Bumper/bumperPlate.SLDPRT
Solidworks/Bumper/bumperPlate_short.SLDPRT
Solidworks/Bumper/bumperSpring_9657K730.SLDPRT
Solidworks/Bumper/laser_cutter_acrylic_base.SLDPRT
Solidworks/Bumper/lasercutter/Bumper.SLDDRW
Solidworks/Bumper/lasercutter/Bumper_back_laser.DXF
Solidworks/Bumper/lasercutter/Bumper_cdw_short.DXF
Solidworks/Bumper/lasercutter/Bumper_corel.DXF
Solidworks/Bumper/lasercutter/Bumper_large.DXF
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

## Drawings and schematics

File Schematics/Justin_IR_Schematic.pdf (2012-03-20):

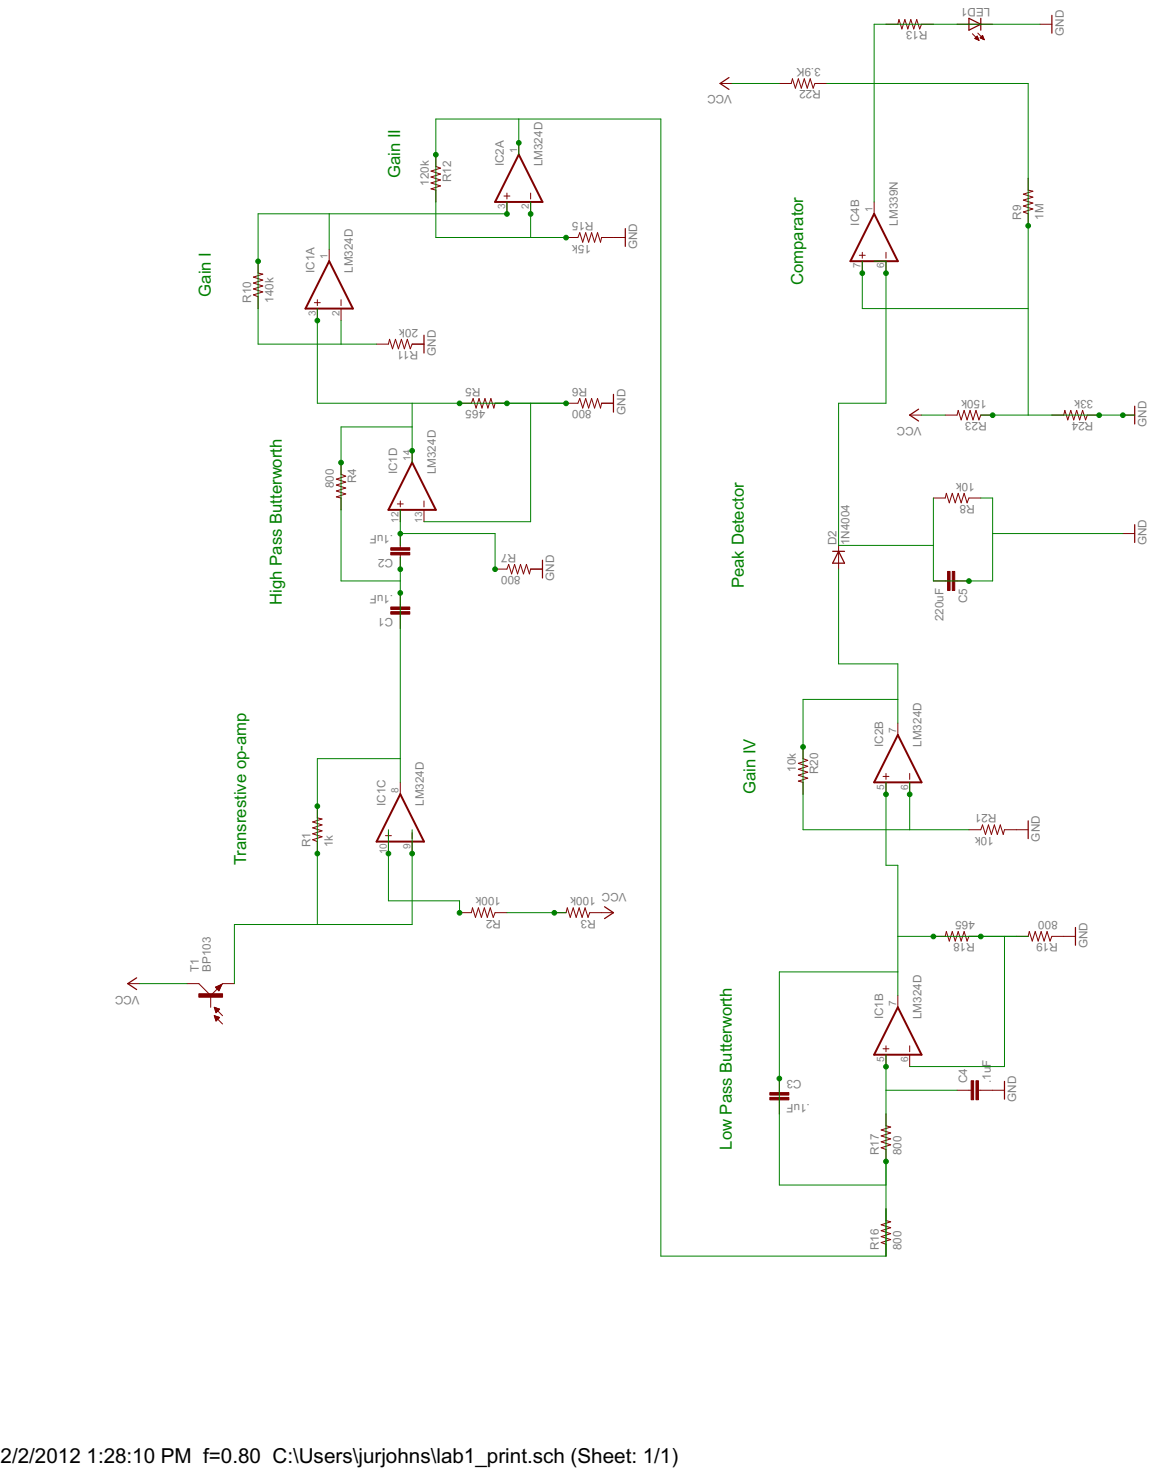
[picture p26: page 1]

High Pass Butterworth Gain I

GND GND

Low Pass Butterworth Gain IV

2/2/2012 1:28:10 PM f=0.80 C:\Users\jurjohns\lab1_print.sch (Sheet: 1/1)

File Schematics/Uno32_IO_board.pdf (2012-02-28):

# The CMPE 118 Uno32 I/O Board

Dept. of Computer Engineering, UCSC

## Background:

The ChipKit Uno32 module is a single-board computer produced by Digilent, Inc., which integrates a Microchip PIC3 microcontroller (PIC32MX320F128H), FTDI USB to Serial converter, voltage regulation, and 3.3V clamp diodes into a tidy little package. CMPE118 uses the Uno32 platform throughout the lab exercises and final project. The Uno32 is an Arduino compatible module, though we reflash the Arduino firmware to use a custom bootloader that allows us to program the PIC32 directly in C over the USB link.

However, the Uno32 wasn’t designed with CMPE118 in mind, so it isn’t exactly what we want, so we’ve designed and manufactured the Uno32 I/O board to get us closer to the ideal we are looking for.

The Uno32 I/O Board has several major functions:

1. Bring out all of the connections from the Uno32 to clearly defined and easily accessible ports with uniform connectors.
2. Provide a wide range of voltage input through an onboard switching regulator (6V to 30V).
3. Provide over-voltage and over-current protection circuitry on all port pins.
4. Provide LED banks for user visual outputs.
5. Provide both local and remote on/off power and reset switches
6. Provide reverse polarity protection
7. Provide fuse protected power distribution for additional circuits.

The data sheet for the ChipKit Uno32 can be found on the Digilentinc.com website at: http://www.digilentinc.com/Products/Detail.cfm?NavPath=2,892,893&Prod=CHIPKIT-UNO32

## Using the CMPE118 Uno32 I/O Board:

Using the CMPE118 Uno32 I/O Board should be straightforward. All the connections that will typically be made to the board are located around the edge of the board, and are clearly labeled and logically grouped. At the end of this document is a table which lists each pin on the PORT, along with its associated pins on the PIC32 microcontroller. All ports are clamped with diodes (TL7226) and series resistors to protect them from either overvoltage, undervoltage, or excessive currents.
Digital Input/Output Ports (PORT-X, PORT-Y, and PORT-Z):
Digital input and output ports are located on the three ports on the top of the board. They can be accessed either directly at the bit level through the #defines in the PORTS library, or as a word sized port through the functions contained within the library. Following the convention that microchip uses, the _TRIS registers are used to set output (0) or input (1) for each pin. The _LAT registers are used to write the output, and the _BIT registers to read from the port.

Port X, Y, and Z each have the outer two pins of the connectors grounded at the I/O board.

The pinout of PORT-X, PORT-Y, and PORT-Z are as follows:
PORT | Connection
Pin 1 | GND
Pin 2 | GND
Pin 3-12 | PORT-x 3-12
Pin 13 | GND
Pin 14 | GND

Digital and Analog Input/Output Ports (PORT-V and PORT-W):
Analog inputs (10bit ADC) are available on PORT-V and PORT-W, and can be set either as Analog or Digital I/O. The Analog pins can be accessed through the AD library, and the digital I/O can be accessed through the PORTS library.

Port V and W each have the outer pins connected to ground, and only have six pins each with the remaining pins connected to ground.

The pinout of PORT-V and PORT-W are as follows:
PORT | Connection
Pin 1 | GND
Pin 2 | GND
Pin 3-8 | PORT-w 3-8
Pin 9 | GND
Pin 10 | GND
Pin 11 | GND
Pin 12 | GND
Pin 13 | GND
Pin 14 | GND

Battery Voltage Monitoring:
The Uno32 I/O Board includes a precision 9:1 voltage divider connected to an ADC pin that is accessible through the AD library.

LED Banks:
The Uno32 I/O Board includes 12 LEDs organized into 3 banks of 4 LEDs each. They are connected to a subset of pins (see table at end) and are accessible through the LED library. The LED CONTROL jumper (JP7) connects the top of each bank of LEDs to the 3.3V rail through a set of current-limiting resistor banks. Leave them open if using them as normal I/O pins

Reset and Remote Reset (SW1 and JP3):
The Uno32 I/O Board includes a reset switch (SW1) as well as a remote reset jumper (JP3). The switch is a momentary contact switch which holds the PIC32 in reset while depressed. The remote switch works by shorting either of the outer pins to the center pin to reset the micro.
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

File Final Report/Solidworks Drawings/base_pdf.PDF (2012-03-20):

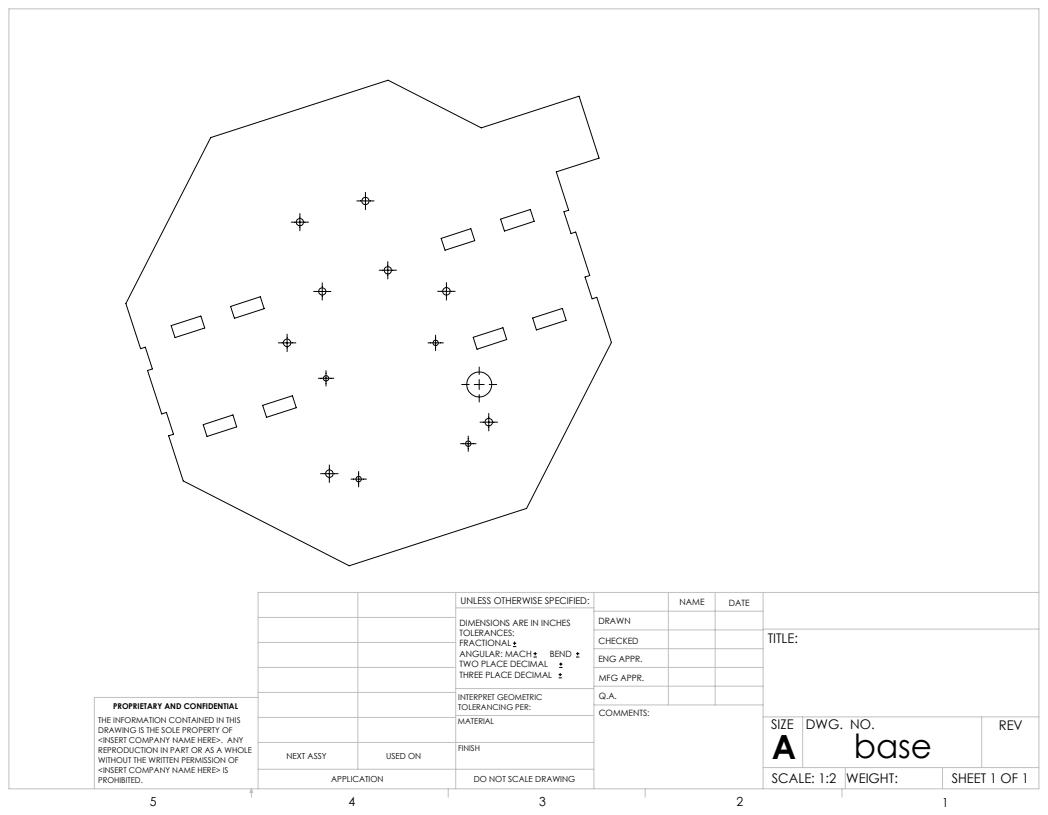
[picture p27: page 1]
SHEET 1 OF 1; SCALE: 1:2 WEIGHT:; DWG. NO.; REV; MFG APPR.; ENG APPR.; INTERPRET GEOMETRIC TOLERANCING PER:; ANGULAR: MACH; BEND; NEXT ASSY; USED ON

UNLESS OTHERWISE SPECIFIED:

DIMENSIONS ARE IN INCHES
TOLERANCES:
FRACTIONAL
TWO PLACE DECIMAL
THREE PLACE DECIMAL

PROPRIETARY AND CONFIDENTIAL
THE INFORMATION CONTAINED IN THIS
DRAWING IS THE SOLE PROPERTY OF
<INSERT COMPANY NAME HERE>. ANY
REPRODUCTION IN PART OR AS A WHOLE
WITHOUT THE WRITTEN PERMISSION OF
<INSERT COMPANY NAME HERE> IS
PROHIBITED.

DO NOT SCALE DRAWING

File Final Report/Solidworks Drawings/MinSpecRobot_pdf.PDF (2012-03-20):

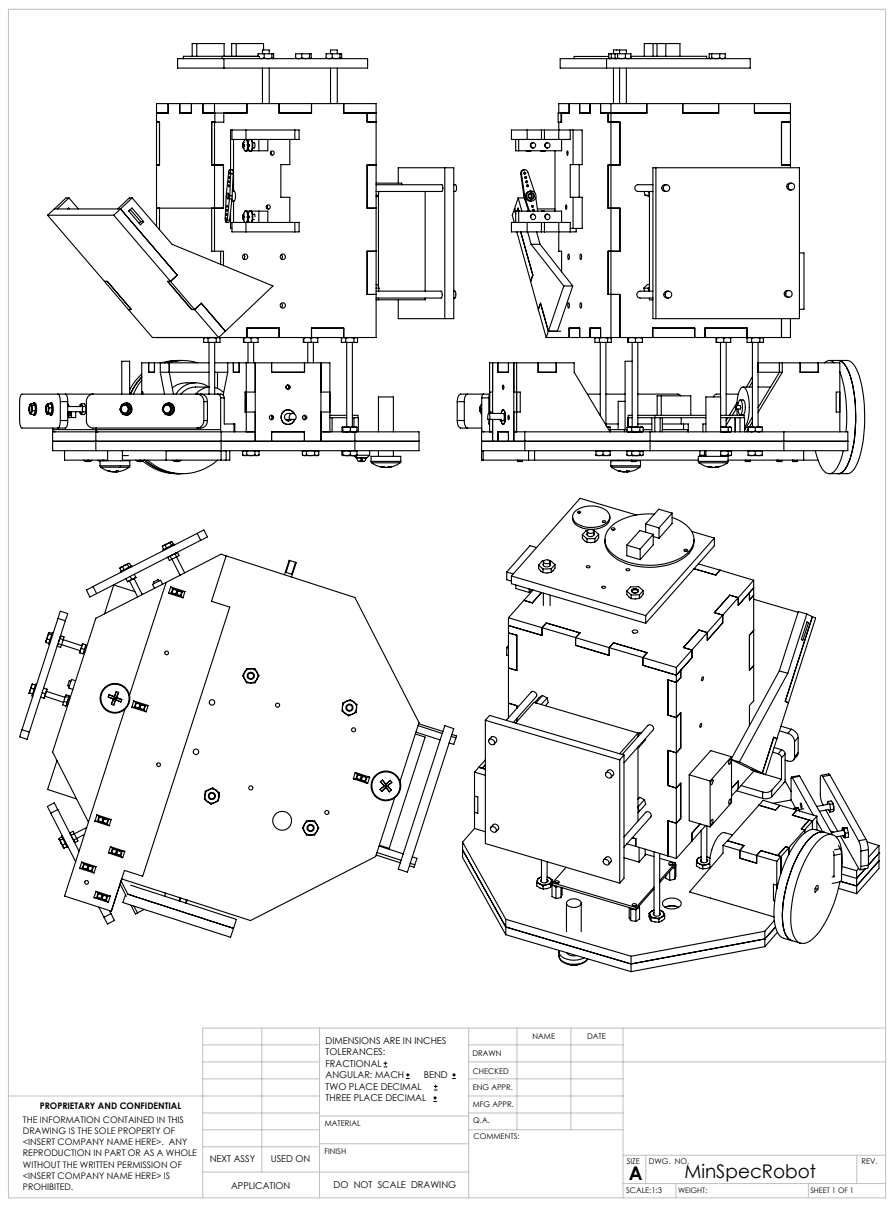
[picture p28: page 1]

TOLERANCES: FRACTIONAL ANGULAR: MACH BEND TWO PLACE DECIMAL THREE PLACE DECIMAL | | NAME | DATE DIMENSIONS ARE IN INCHES

DRAWN
CHECKED
ENG APPR.

PROPRIETARY AND CONFIDENTIAL THE INFORMATION CONTAINED IN THIS DRAWING IS THE SOLE PROPERTY OF <INSERT COMPANY NAME HERE>. ANY REPRODUCTION IN PART OR AS A WHOLE WITHOUT THE WRITTEN PERMISSION OF <INSERT COMPANY NAME HERE> IS PROHIBITED. | | | MFG APPR.

MATERIAL | Q.A.

NEXT ASSY | USED ON | FINISH

SIZE A | DWG. NO. MinSpecRobot | REV.

APPLICATION | | DO NOT SCALE DRAWING

SCALE:1:3 | WEIGHT: | SHEET 1 OF 1

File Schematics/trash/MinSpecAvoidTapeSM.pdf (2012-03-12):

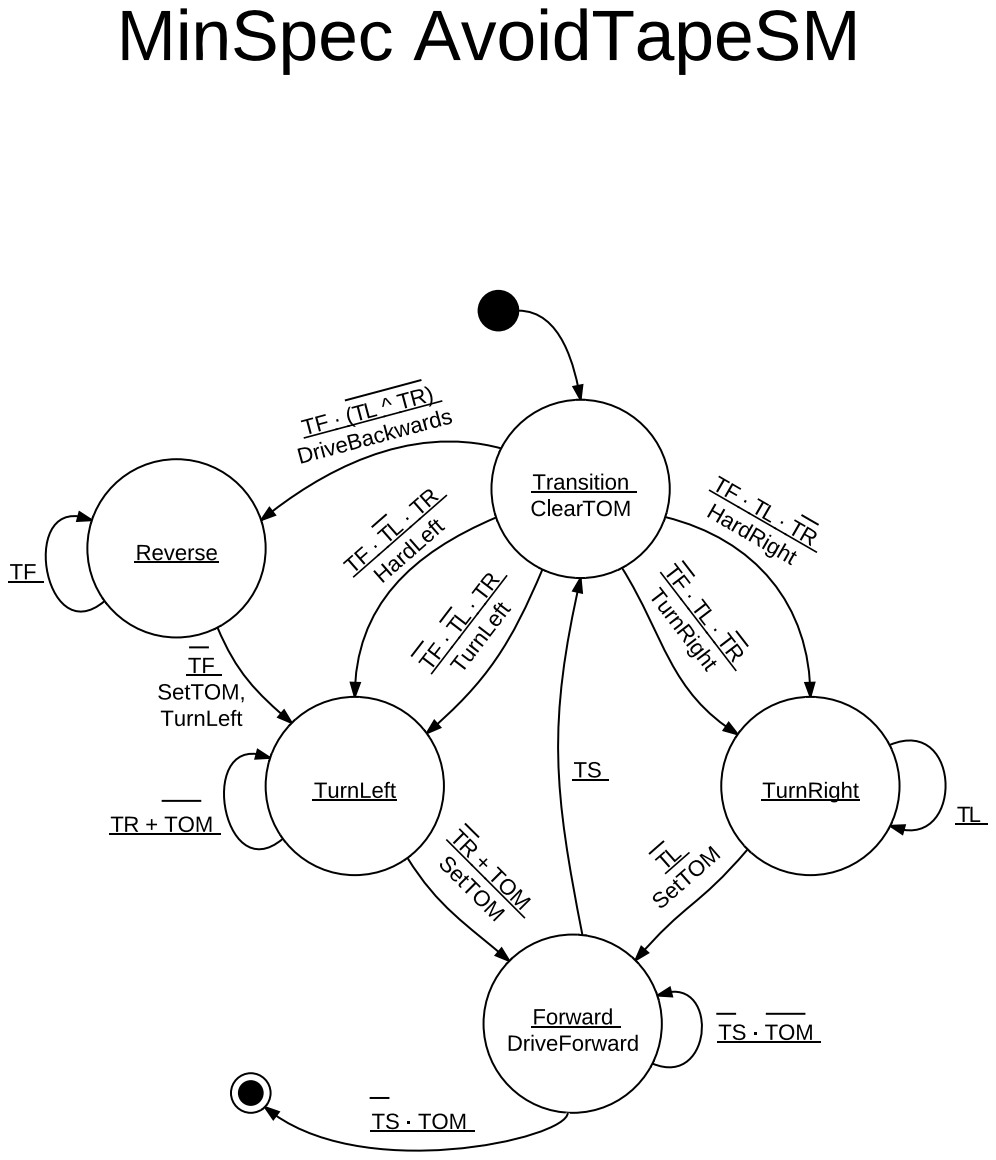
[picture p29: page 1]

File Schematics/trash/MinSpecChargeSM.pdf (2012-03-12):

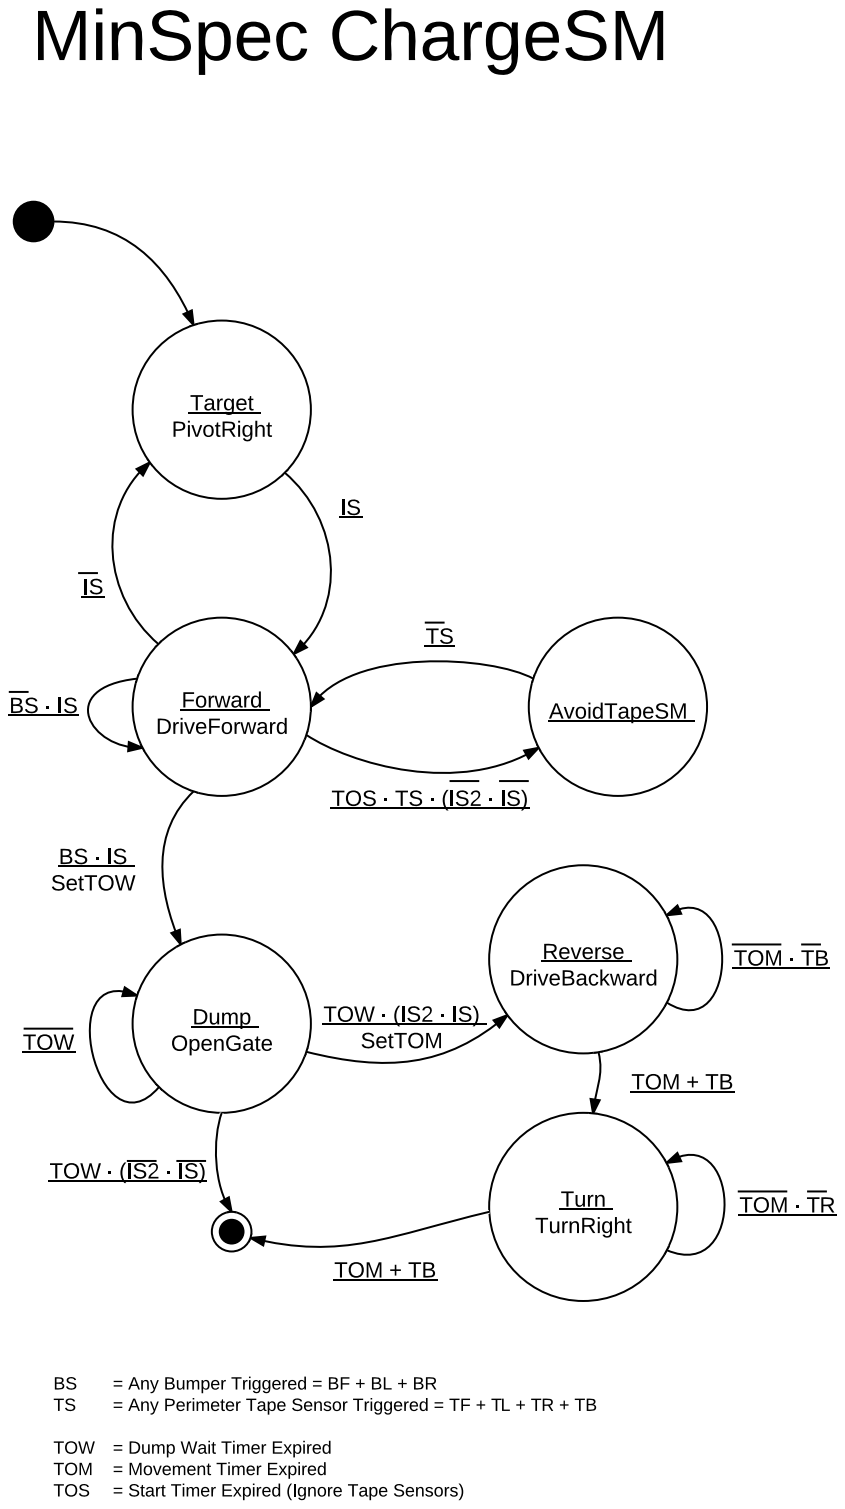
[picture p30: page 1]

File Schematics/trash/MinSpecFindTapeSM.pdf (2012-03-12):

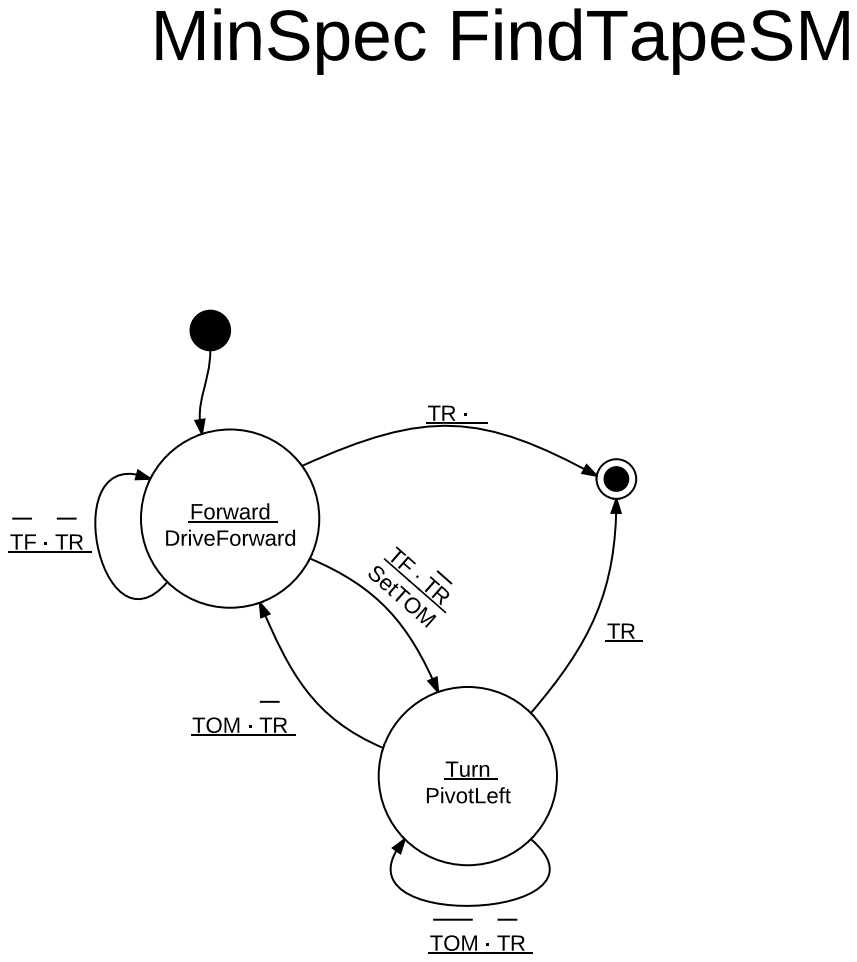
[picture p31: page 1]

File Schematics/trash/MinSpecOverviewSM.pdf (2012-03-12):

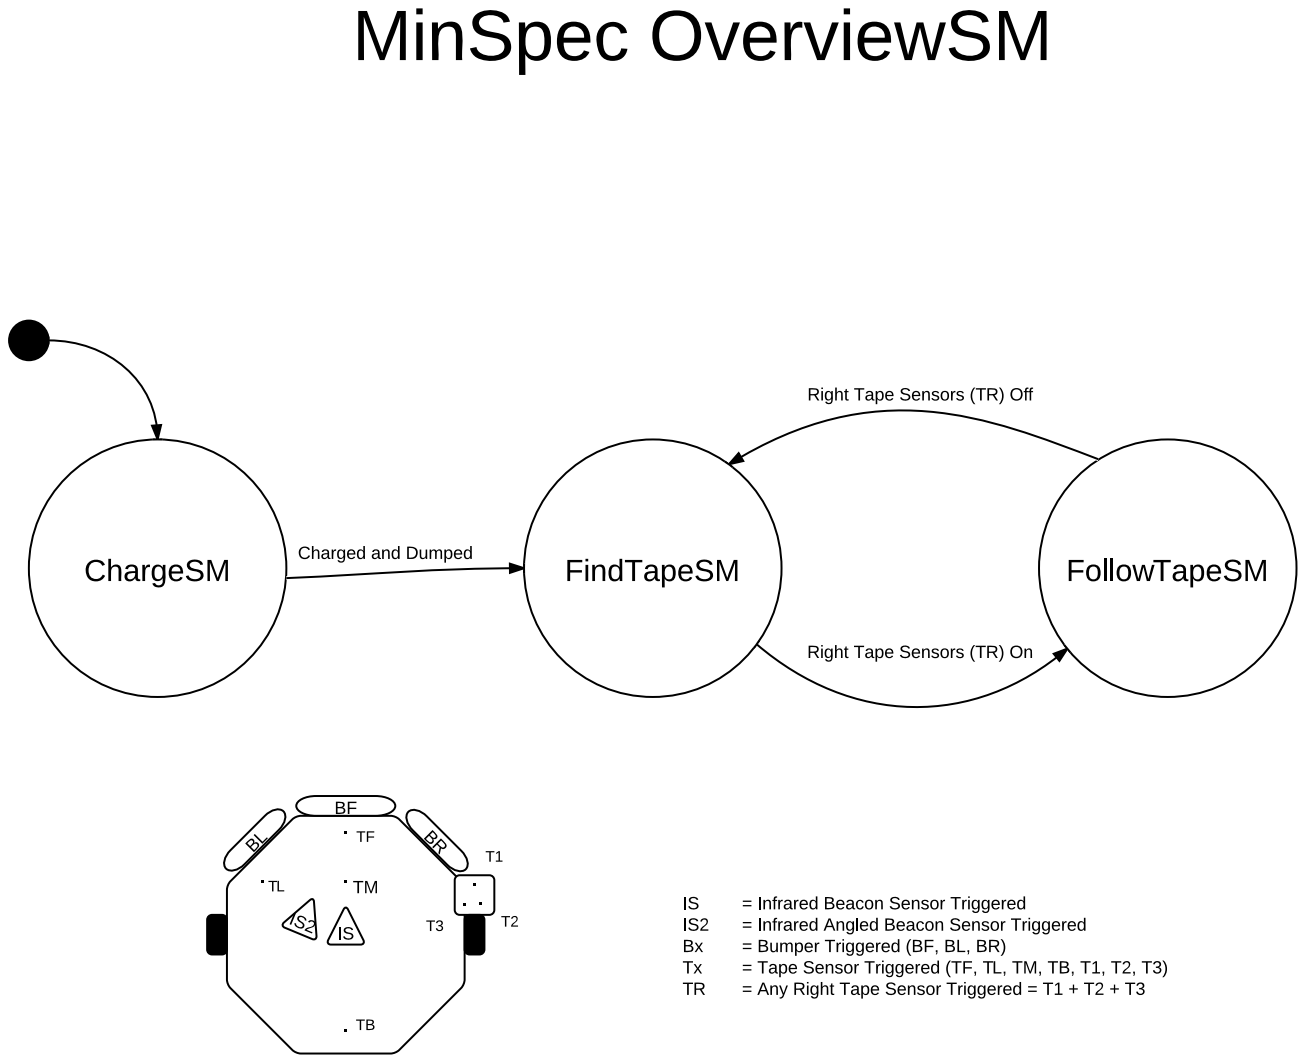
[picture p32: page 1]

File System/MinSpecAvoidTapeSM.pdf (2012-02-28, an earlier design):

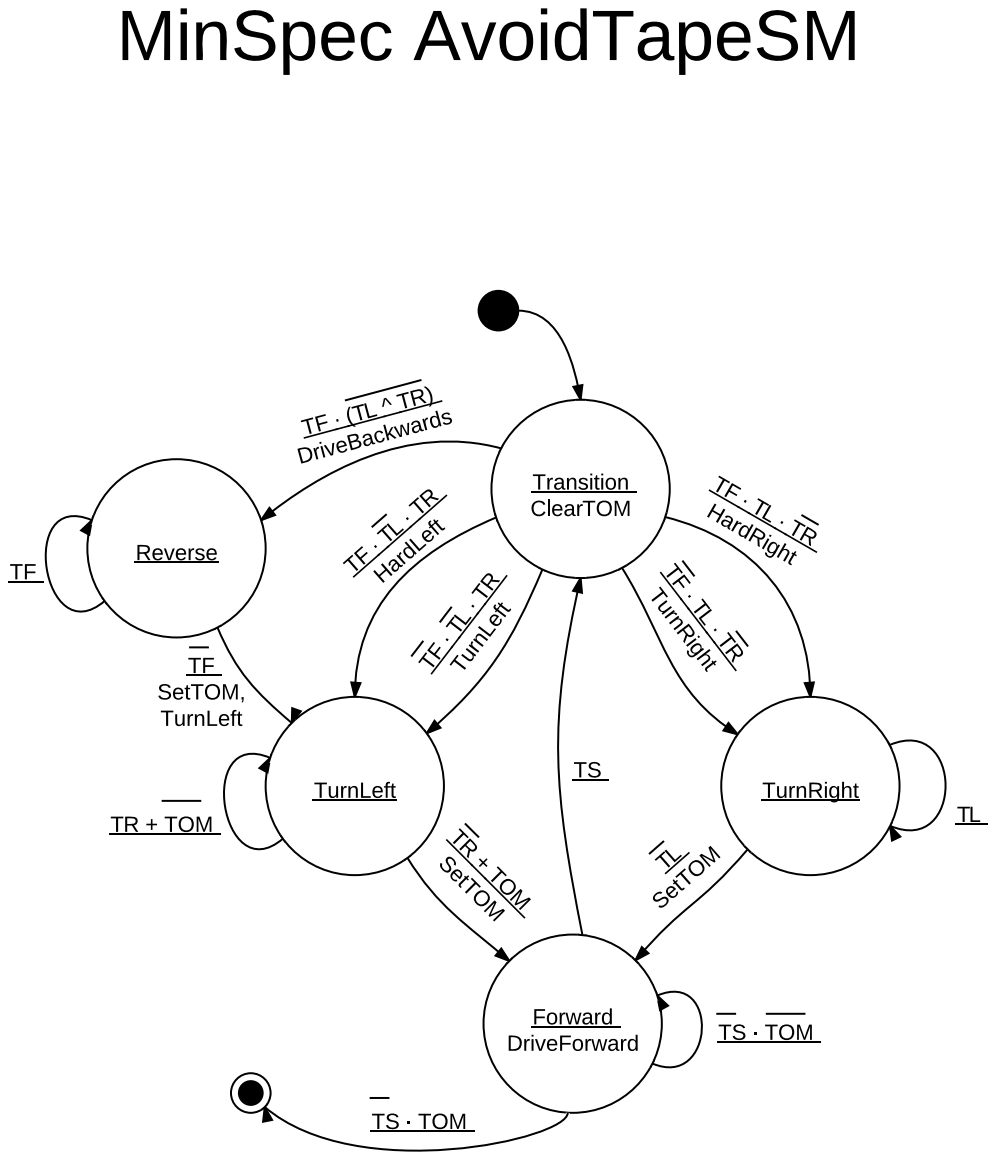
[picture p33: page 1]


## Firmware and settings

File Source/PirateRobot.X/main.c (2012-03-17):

/*
 * File:   main.c
 * Author: dagoodma
 *
 * Created on February 21, 2012, 7:46 PM
 */

#define USE_MAIN

//#define DEBUG


//#define DEBUG_STATES // slows and blinks LEDs
//#define DISABLE_AVOID
//#define DEBUG_VERBOSE

//#define TAPE_CALIBRATE 1

//#define TARGET_USETIME




#ifdef USE_MAIN
#include <p32xxxx.h>
#include "serial.h"
#include "PORTS.h"
#include "timers.h"
#include "Drive.h"
#include "Gate.h"
#include "TapeSensor.h"
#include "IR_new.h"
#include "Bumper.h"
#include "AD.h"
#include "Util.h"
#include "LED.h"
//#include <stdio.h>


/*******************************************************************************
 * #DEFINES                                                                    *
 ******************************************************************************/
#define TIMER_START 6
#define TIMER_MOVE 7
#define TIMER_AVOID 8
#define TIMER_FIND 9
#define TIMER_FOLLOW 10
#define TIMER_CALIBRATE 11
#define TIMER_RETURN 12
#define TIMER_CHARGE 13
#define TIMER_OBSTACLE 14
#define MASTER_TIMER 15

#define MASTER_TIMEOUT 11000

#define START_DELAY 2500

#define CHARGE_DUMP_DELAY 800
#define CHARGE_REVERSE_DELAY 1750
#define CHARGE_TURN_DELAY 620
#define CHARGE_START_DELAY 1550

#define AVOID_FORWARD_DELAY 2750
static int avoidForwardDelay = AVOID_FORWARD_DELAY;
#define AVOID_TIMEOUT 4600
#define AVOID_REVERSE_DELAY 1300
#define AVOID_TURN_DELAY 1000
#define AVOID_BACK_DELAY 1700
#define AVOID_CHECK_DELAY 450

#define OBSTACLE_TURN_DELAY 1000
#define OBSTACLE_FORWARD_DELAY 2750
static int obstacleForwardDelay = OBSTACLE_FORWARD_DELAY;
#define OBSTACLE_REVERSE_DELAY 1300


#define LEFT_SEARCH_TIME 2750 // time before trying other direction

#define FIND_TURN_TIMEOUT 2900 // time til turn gives up
#define FIND_TURN_DELAY 790 // time to start checking right arm

#define FOLLOW_SEARCH_TIMEOUT 3000 // time to give up right turn
#define FOLLOW_ACUTE_DELAY 750
#define FOLLOW_ACUTE_TIMEOUT 5200

#define CALIBRATE_DELAY 1500
#define CALIBRATE_TIMEOUT 7600

#define CALIBRATE_INDICATOR PORTY06_LAT
#define CALIBRATE_INDICATOR_TRIS PORTY06_TRIS
#define CALIBRATE_TAPEHIGHEST_I TAPE_ARMFRONT_I
#define CALIBRATE_TAPELOWEST_I TAPE_ARMFRONT_I

#define RETURN_LEFT_DELAY 745 // time to turn left for 90 deg
#define RETURN_RIGHT_DELAY 2550 //time to turn right on left wall rebound
#define RETURN_TAPE_DELAY 2000 // time to ignore tape sensor triggers


/*******************************************************************************
 * VARIABLES                                                                   *
 ******************************************************************************/

//---------- Top state variables ------------
static enum { calibrate, target, charge, find_tape, follow_tape, return_island, hold} topState;
//static enum { none, acquired_target, lost_target, dumped, arm_on, found_island} topEvent = none;

//-------- Target state variables -----------

static unsigned int highestIRSeen = 0;
static unsigned int highestIRTime = 0;
static enum { target_findmaxleft, target_findmaxright, target_returnmax } targetState = target_findmaxleft;
static enum { target_none, target_timedout, target_highestpast, target_foundmax } targetEvent = target_none;

static unsigned char *targetStates[] = { "target_findmaxleft", "target_findmaxright", "target_returnmax" };
static unsigned char *targetEvents[] = { "target_none", "target_timedout", "target_highestpast", "target_foundmax" };

/*
static enum { target_searchleft, target_searchright, target_acquired } targetState = target_searchleft;
static enum { target_none, target_timedout, target_found, target_lost } targetEvent = target_none;
 */

//-------- Charge state variables -----------
static enum { charge_forward, charge_dump, charge_reverse, charge_turn,
        charge_avoidtape} chargeState = charge_forward;
static enum { charge_none, charge_lostbeacon, charge_hit, charge_hittape,
        charge_blocked, charge_finished, charge_avoided, charge_reversed } chargeEvent = charge_none;\
static char neverCharged = 1;

//-------- AvoidTape state variables -----------
static enum { avoid_transition, avoid_forward, avoid_left, avoid_right, avoid_back } avoidState = avoid_transition;
static enum { avoid_none, avoid_goleft, avoid_forwarded, avoid_goright, avoid_goback, avoid_cleared } avoidEvent = avoid_none;


static unsigned char *avoidStates[] = { "avoid_transition", "avoid_reverse", "avoid_turnleft", "avoid_turnright",
        "avoid_forward", "avoid_revturnleft", "avoid_bump"};
static unsigned char *avoidEvents[] = { "avoid_none", "avoid_goback", "avoid_cutright", "avoid_goright",
    "avoid_goleft", "avoid_cutleft", "avoid_reversed", "avoid_lefted", "avoid_righted",
    "avoid_forwarded", "avoid_timedout", "avoid_failed", "avoid_revover", "avoid_bumped"};

//-------- FindTape state variables -----------
static enum { find_forward, find_turn, find_avoidobstacle } findState = find_forward;
static enum { find_none, find_foundfront, find_hit, find_avoided, find_found, find_timedout } findEvent = find_none;
static unsigned char *findStates[] = { "find_forward", "find_turn" };
static unsigned char *findEvents[] = { "find_none", "find_foundfront", "find_found", "find_timedout" };

//-------- FollowTape state variables -----------
static enum { follow_transition, follow_avoidobstacle, follow_hardleft, follow_left,
        follow_hardright, follow_right, follow_forward, follow_acuteleft, follow_searchleft,
        follow_searchright } followState = follow_transition;
static enum { follow_none, follow_hit, follow_rightfrontoff, follow_rightoff,
        follow_leftfrontoff, follow_leftoff, follow_armon, follow_losttape,
        follow_foundisland, follow_foundacute, follow_acuted, follow_avoided, follow_searchfailed,
        follow_lookleft, follow_lookright, follow_foundfront, follow_acutefailed } followEvent = follow_none;

static unsigned char *followStates[] = { "follow_transition", "follow_avoidobstacle", "follow_hardleft", "follow_left",
        "follow_hardright", "follow_righ", "follow_forward", "follow_acuteleft", "follow_searchleft",
        "follow_searchright" };

static unsigned char *followEvents[] = { "follow_none", "follow_hit", "follow_rightfrontoff", "follow_rightoff",
        "follow_leftfrontoff", "follow_leftoff", "follow_armon", "follow_losttape",
        "follow_foundisland", "follow_foundacute", "follow_acuted", "follow_avoided", "follow_searchfailed",
        "follow_lookleft", "follow_lookright", "follow_foundfront", "follow_acutefailed" };

//-------- AvoidObstacle state variables -----------
static enum { obstacle_transition, obstacle_left, obstacle_right, obstacle_back, obstacle_opposite, obstacle_forward }
    obstacleState = obstacle_transition;
static enum { obstacle_none, obstacle_goleft, obstacle_goright, obstacle_goback, obstacle_cleared, obstacle_forwarded,
    obstacle_backed } obstacleEvent = obstacle_none;

static enum { return_left, return_forward, return_avoidobstacle, return_right, return_uturn } returnState = return_left;
static enum { return_none, return_lefted, return_hitobstacle, return_hitwall, return_hittape, return_uturned,
        return_righted, return_goright } returnEvent = return_none;

        static unsigned char *returnStates[] = { "return_left", "return_forward", "return_avoidobstacle", "return_right", "return_uturn" };
static unsigned char *returnEvents[] = { "return_none", "return_lefted", "return_hitobstacle", "return_hitwall", "return_armon", "return_uturned",
        "return_righted", "return_goright" };


static enum {calibrate_onthreshold, calibrate_offthreshold} calibrateState = calibrate_onthreshold;
static enum { calibrate_none, calibrate_ready, calibrate_timedout, calibrate_next, calibrate_finished } calibrateEvent = calibrate_none;

static int time;

#define START_STATE target


/*******************************************************************************
 * FUNCTION  PROTOTYPES                                                        *
 ******************************************************************************/
void HandleTopSM();

void DuringCalibrateSM();
void DuringChargeSM();
void DuringTargetSM();
void DuringAvoidTapeSM();
void DuringFindTapeSM();
void DuringFollowTapeSM();
void DuringAvoidObstacleSM();
void DuringReturnIslandSM();

void UpdateChargeEvent();
void UpdateAvoidTapeEvent();
void UpdateTargetEvent();
void UpdateFindTapeEvent();
void UpdateFollowTapeEvent();
void UpdateAvoidObstacleEvent();
void UpdateCalibrateEvent();
void UpdateReturnIslandEvent();
void UpdateCalibrateEvent();

void InitStartState();
void InitCalibrateSM();
void InitChargeSM();
void InitTargetSM();
void InitAvoidTapeSM();
void InitFindTapeSM();
void InitFollowTapeSM();
void InitReturnIslandSM();
void InitAvoidObstacleSM();
// void InitFollowAcuteSM();



// -------- others -------
void wait();
unsigned int DecrementTimer(unsigned int timeMax, unsigned int timeCur);

void DuringReturnIslandSM() {

#ifdef DEBUG
     //printf("\nReturn  STATE=%u EVENT=%u", returnState, returnEvent);
#endif
    UpdateReturnIslandEvent();

    switch(returnState) {
        case return_left:
            //printf("A");
            if (returnEvent == return_lefted) {
                //InitTimer(TIMER_RETURN, RETURN_COLLIDE_TIMEOUT);
                InitTimer(TIMER_RETURN, RETURN_TAPE_DELAY);
                returnState = return_forward;
            }
            else {
                Drive_Turn(pivot, left, HALF_SPEED);
            }
            break;
        case return_forward:
            //printf("B");
            if (returnEvent == return_hitobstacle) {
                returnState = return_avoidobstacle;
                InitAvoidObstacleSM();
            }
            else if (returnEvent == return_hittape) {
                // EXIT caller picks this up
                Drive_Stop();
            }
            /*
            else if (returnEvent == return_hitwall) {
                returnState = return_uturn;
                InitTimer(TIMER_RETURN,RETURN_LEFT_DELAY);
            }
             * */

            else if (returnEvent == return_goright) {
                returnState = return_right;
                InitTimer(TIMER_RETURN, RETURN_RIGHT_DELAY);
            }
            else {

                Drive_Forward(HALF_SPEED);
            }
            break;
        case return_avoidobstacle:
            //printf("C");
            DuringAvoidObstacleSM();
            if (avoidEvent == obstacle_forwarded) {
                returnState = return_forward;
            }
            break;
        case return_right:
            //printf("D");
            if (returnEvent == return_righted)
                returnState = return_forward;
            else
                Drive_Turn(soft,right,HALF_SPEED);
            break;
         /*
        case return_uturn:
            if (returnEvent == return_uturned)
                returnState = return_forward;
            else
                Drive_Turn(pivot, right, MID_SPEED);
            break;
       */
    } // switch
}

void UpdateReturnIslandEvent() {
    returnEvent = return_none;


    switch(returnState) {
        case return_left:
            if (IsTimerExpired(TIMER_RETURN))
                returnEvent = return_lefted;
            break;
        case return_forward:
            if (Bumper_AnyTriggered())
                returnEvent = return_hitobstacle;
            else if ((Tape_ArmLeftTriggered() || Tape_ArmRightTriggered() || Tape_ArmFrontTriggered() ||
                    Tape_RightTriggered() || Tape_CenterTriggered()) && IsTimerExpired(TIMER_RETURN))
            //else if (Tape_AnyTriggered() && IsTimerExpired(TIMER_MOVE))
                returnEvent = return_hittape;
            /**
            else if (IsTimerExpired(TIMER_RETURN) && Bumper_AnyTriggered())
                returnEvent = return_hitwall;
             **/
            else if (Tape_LeftTriggered() && IsTimerExpired(TIMER_RETURN))
                returnEvent = return_goright;
            break;
        case return_avoidobstacle:
            break;
        case return_right:
            if (IsTimerExpired(TIMER_RETURN))
                returnEvent = return_righted;
            break;
            /*
        case return_uturn:
            if (IsTimerExpired(TIMER_RETURN))
                returnEvent == return_uturned;
            break;
             * */
    } // switch
}

void DuringAvoidObstacleSM() {
    UpdateAvoidObstacleEvent();
    #ifdef DEBUG
     //printf("\nObstacle  STATE=%u EVENT=%u", obstacleState, obstacleEvent);
#endif

    switch(obstacleState) {
        case obstacle_transition:
            //printf("A");
            if (obstacleEvent == obstacle_goleft) {
                InitTimer(TIMER_OBSTACLE, OBSTACLE_TURN_DELAY);
                Drive_Turn(pivot, left, HALF_SPEED);
                obstacleState = obstacle_left;
            }
            else if (obstacleEvent == obstacle_goright) {
                InitTimer(TIMER_OBSTACLE, OBSTACLE_TURN_DELAY);
                Drive_Turn(pivot, right, HALF_SPEED);
                obstacleState = obstacle_right;
            }
            else if (obstacleEvent == obstacle_goback) {
                InitTimer(TIMER_OBSTACLE, OBSTACLE_REVERSE_DELAY);
                Drive_Reverse(HALF_SPEED);
                obstacleState = obstacle_back;
            }
            else {
                // EXIT -- caller handles
                obstacleEvent = obstacle_forwarded;
            }
            break;
        case obstacle_forward:
            //printf("B");
            if (obstacleEvent == obstacle_forwarded) {
                obstacleState = obstacle_transition;
            }
            break;
        case obstacle_back:
            //printf("C");
            if (obstacleEvent == obstacle_backed) {
                InitTimer(TIMER_OBSTACLE, OBSTACLE_TURN_DELAY);
                Drive_Turn(pivot,opposite,HALF_SPEED);
                obstacleState = obstacle_opposite;
            }
            break;
        default:
            //printf("D");
            // obstacle_opposite, left, right
            if (obstacleEvent == obstacle_cleared) {
                obstacleState = obstacle_forward;
                Drive_Forward(HALF_SPEED);
                obstacleForwardDelay = DecrementTimer(OBSTACLE_FORWARD_DELAY, obstacleForwardDelay);
                InitTimer(TIMER_OBSTACLE, obstacleForwardDelay);
            }
            break;


    /*
    switch(obstacleState) {
        case obstacle_reverse:
            if (obstacleEvent == obstacle_reversed) {
                InitTimer(TIMER_MOVE, OBSTACLE_TURN_DELAY);
                obstacleState = obstacle_turnleft;
            }
            else {
                Drive_Reverse(HALF_SPEED);
            }
            break;
        case obstacle_turnleft:
            if (obstacleEvent == obstacle_lefted) {
                InitTimer(TIMER_MOVE,OBSTACLE_FORWARD_DELAY);
                obstacleState = obstacle_forward;
            }
            else {
                Drive_Turn(pivot, left, HALF_SPEED);
            }
            break;
        case obstacle_forward:
            if (obstacleEvent == obstacle_forwarded) {
                InitTimer(TIMER_MOVE,OBSTACLE_TURN_DELAY);
                obstacleState = obstacle_turnright;
            }
            else {
                Drive_Forward(HALF_SPEED);
            }
            break;
        case obstacle_turnright:
            if (obstacleEvent == obstacle_righted) {
                InitTimer(TIMER_MOVE,OBSTACLE_FORWARD2_DELAY);
                obstacleState = obstacle_forward2;
            }
            else {
                Drive_Turn(pivot, right, HALF_SPEED);
            }
            break;
        case obstacle_forward2:
            if (obstacleEvent == obstacle_forwarded) {
                InitTimer(TIMER_MOVE,OBSTACLE_TURN2_DELAY);
                obstacleState = obstacle_turnright2;
            }
            else {
                Drive_Forward(HALF_SPEED);
            }
            break;
        case obstacle_turnright2:
            if (obstacleEvent == obstacle_avoided) {
                // EXIT -- caller handles this
                Drive_Stop();
            }
            break;
     */

    } // switch
}
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
int main(void) {

    // ---------------------------- Initialization ----------------------------
    SERIAL_Init();
    TIMERS_Init();

    // Initialize interrupts
    INTEnableSystemMultiVectoredInt();
      time = GetTime();

     // Initialize AD system
    /*
    if ( AD_Init(TAPE_LEFT | TAPE_CENTER | TAPE_RIGHT | TAPE_BACK |
        TAPE_ARMFRONT | TAPE_ARMLEFT | TAPE_ARMRIGHT | IR_PINS | BAT_VOLTAGE )
            == SUCCESS) {

#ifdef DEBUG
         //db//printf("\nADC initialized successfully.");
#endif
    }
    else {

#ifdef DEBUG
         //db//printf("\nADC failed to initialize.");
#endif
    }
     */
    int adPins = TAPE_LEFT | TAPE_CENTER | TAPE_RIGHT | TAPE_BACK |
         TAPE_ARMFRONT | TAPE_ARMLEFT | TAPE_ARMRIGHT | BAT_VOLTAGE | IR_PINS;

    AD_Init(adPins);

#ifdef DEBUG
     ////printf("\nPins=%x", adPins);
#endif

    // Initialize modules
    IR_Init();
    Tape_Init();
    Drive_Init();
    Bumper_Init();
    Gate_Init();

     time = GetTime();

    // Initialize state machine


#ifdef TAPE_CALIBRATE
    InitCalibrateSM();
        
    topState = calibrate;
#else

    
#endif

    InitTimer(TIMER_START, START_DELAY);

     while (!IsTimerExpired(TIMER_START)) {
        Tape_HandleSM();
        Drive_Update();
        Bumper_Update();
        IR_Update();

        if (Bumper_AnyTriggered()) {
            /*
            Drive_Turn(pivot,left,HALF_SPEED);
            wait();
            Drive_Turn(pivot,right,HALF_SPEED);
            wait();
            Drive_Turn(pivot,left,HALF_SPEED);
            wait();
            Drive_Turn(pivot,right,HALF_SPEED);
            wait();
            Drive_Reverse(FULL_SPEED);
            wait();
            Drive_Forward(FULL_SPEED);
             */
            wait();

            topState = hold;
            
        }

        if (topState == hold) {
                goto exit;
        }
     }

    InitStartState();

#ifdef DEBUG
     //printf("\nReady, set...");
    wait();
     //printf(" Go!");

     //db//printf("\nHello, I am working...");
#endif





    // ------------------------------- Main Loop -------------------------------
    while (1) {
        // Handle updates and module state machines
        Tape_HandleSM();
        Drive_Update();
        Bumper_Update();
        IR_Update();
        
        HandleTopSM();


        


#ifdef DEBUG
         ////printf("\nTopSTATE! %u", topState);
#endif

        if (topState == hold) {
                goto exit;
            }

       //while (!IsTransmitEmpty()); // bad, this is blocking code

    }
    exit:
    Tape_End();
    Drive_Stop();
    Bumper_End();
    Gate_End();
    IR_End();

    return 0;
} // end of main()

void InitStartState() {
    topState = START_STATE;
    switch (START_STATE) {
        case charge:
            InitChargeSM();
            break;
        case find_tape:
            InitFindTapeSM();
            break;
        case follow_tape:
            InitFollowTapeSM();
            break;
        case target:
            InitTargetSM();
            break;

    } // switch
}


void InitChargeSM() {
    if (neverCharged) {
        InitTimer(TIMER_CHARGE, CHARGE_START_DELAY);
        neverCharged = 0;
    }
    ClearTimerExpired(TIMER_MOVE);
    chargeState = charge_forward;
}

void InitFollowTapeSM() {
    followState = follow_transition;
    InitTimer(TIMER_FOLLOW,1);
}

void InitCalibrateSM() {
    calibrateState = calibrate_onthreshold;

#ifdef DEBUG
//     //printf("\nReady for on tape threshold calibration. Trigger front bumper when done.");
#endif
    InitTimer(TIMER_CALIBRATE, CALIBRATE_TIMEOUT);
    CALIBRATE_INDICATOR_TRIS = 0;
    CALIBRATE_INDICATOR = 0;
}

void InitFindTapeSM() {
    findState = find_forward;
    InitTimer(MASTER_TIMER,MASTER_TIMEOUT);
}

void InitAvoidObstacleSM() {
    obstacleState = obstacle_transition;
}

void InitReturnIslandSM() {
    returnState = return_left;
    InitTimer(TIMER_RETURN, RETURN_LEFT_DELAY);
}

void InitTargetSM() {

    targetState = target_findmaxleft;
    highestIRSeen = 0;
    highestIRTime = 0;
    /*
    targetState = target_searchleft;
    InitTimer(TIMER_MOVE, TARGET_FIRST_SEARCH_TIME);
     */
    InitTimer(TIMER_MOVE, LEFT_SEARCH_TIME);
}

void InitAvoidTapeSM() {
    //tryedAvoiding = 0;
    avoidState = avoid_transition;
    //InitTimer(TIMER_AVOID, AVOID_TIMEOUT);
}

/**
* Function: wait
* @return Nothing
* @remark Waits a small period of time
*/
void wait() {
    unsigned int wait = 0;
    for (wait = 0; wait <= 1000000; wait++)
        asm("nop");
}

unsigned int DecrementTimer(unsigned int timeMax, unsigned int timeCur) {
    int time = timeCur - (timeMax >> 2);
    if (time < 0)
        return timeMax;
    else
        return (unsigned int)time;
}

// ---------------------- EOF ----------------------
#endif

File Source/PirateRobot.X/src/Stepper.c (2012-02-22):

/*
 * File:   Stepper.c
 * Author: Elkaim
 *
 * Created on January 2, 2012, 9:49 PM
 */

#include <p32xxxx.h>
#include <plib.h>

#include "Stepper.h"
#include "Serial.h"
#include "PORTS.h"


/*******************************************************************************
 * PRIVATE #DEFINES                                                            *
 ******************************************************************************/
//#define STEPPER_TEST
//#define DEBUG_VERBOSE
#ifdef DEBUG_VERBOSE
    #define dbprintf(...) printf(__VA_ARGS__)
#else
    #define dbprintf(...)
#endif


/* Note that you need to set the prescalar and periferal clock appropriate to
 * the processor board that you are using. In order to calculate the minimal
 * prescalar: Prescalar = (2000*F_PB/(1000000*0xFFFF))+1, round down */
#ifndef F_CPU
#define F_CPU       80000000L
#define F_PB        (F_CPU/2)
#define F_PB_DIV8   (F_PB/8)
#define F_PB_DIV64  (F_PB/64)
#define ONE_KHZ_RATE  (F_PB_DIV8-1)/1000
#endif

#define MED_HZ_RATE 77
#define LOW_HZ_RATE 10
#define LOW_REP_NUM 64
#define TWENTY_KILOHERTZ 20000

#define LED_BANK1_3 LATDbits.LATD6
#define LED_BANK1_2 LATDbits.LATD11
#define LED_BANK1_1 LATDbits.LATD3
#define LED_BANK1_0 LATDbits.LATD5


#define ShutDownDrive() (COIL_A_ENABLE = 0, COIL_B_ENABLE = 0)
#define TurnOnDrive() (COIL_A_ENABLE = 1, COIL_B_ENABLE = 1)

/*******************************************************************************
 * PRIVATE STRUCTS and TYPEDEFS                                                *
 ******************************************************************************/
//integer round: (x - 1)/y + 1
/*******************************************************************************
 * PRIVATE VARIABLES                                                           *
 ******************************************************************************/

static int stepCount = 0;
static unsigned short int overflowReps = 0;
static unsigned char stepDir = FORWARD;
static enum {off,inited,full,wave,half,halted,waiting} stepperState = off;
static enum {step_one,step_two,step_three,step_four,step_five,
             step_six, step_seven, step_eight} coilState = step_one;

#define STEPPER_MODE wave
#define STEPPER_SPEED 250
//#define STEPPER_RAMPS



static unsigned short int stepSpeed = STEPPER_SPEED;

/*******************************************************************************
 * PRIVATE FUNCTIONS PROTOTYPES                                                *
 ******************************************************************************/
/**
 * @Function: CalculateOverflowPeriod(unsigned short int rate);
 * @param pulse rate is steps per second (0 = 0.5Hz, special case)
 * @return period overflow for timer to match step rate
 * @remark Calculates the overflow period and sets the module variable
 *         overflowReps to match for the right step rate.
 *         Note: rate 0 is a special case corresponding to 0.5Hz
 * @author Gabriel Hugh Elkaim
 * @date 2012.01.28 23:21 */
unsigned short int CalculateOverflowPeriod(unsigned short int rate);

/*******************************************************************************
 * PUBLIC FUNCTIONS                                                           *
 ******************************************************************************/

/* There are three possibilities for the step rate calculation that keep the
   step rate error to under 0.2% of the desired value, from within 0.5 to 2KHz:
   from 78 to 20Khz, Prescale is 1:8, Rollover = (F_PB/8-1)/PPS
   from 10 to 77Hz, Prescale is 1:64, Rollover = (F_PB/64-1)/PPS
   from 0.5 to 10Hz, Set rollover for a constant 1Khz, and increment to reach
   the desired time, Prescale is 1:8, Rollover = (F_PB/8-1)/1000 and the number
   of times to repeat is (1000-1)/PPS + 1                                     */
char Stepper_Init(unsigned short int rate)
{
    unsigned short int overflowPeriod;
    if (rate > TWENTY_KILOHERTZ) return ERROR;
    dbprintf("\nInitializing Stepper Module");
    stepCount = 0;
    overflowReps = 0;
    // Initialize hardware (no current flow)
    COIL_A_DIRECTION = 1;
    COIL_B_DIRECTION = 1;
    ShutDownDrive();
    TRIS_COIL_A_DIRECTION = 0;
    TRIS_COIL_A_ENABLE = 0;
    TRIS_COIL_B_DIRECTION = 0;
    TRIS_COIL_B_ENABLE = 0;
    // Calculate overflow time and prescalar
    overflowPeriod = CalculateOverflowPeriod(rate);
    dbprintf("\nOverflow Period: %u",overflowPeriod);
    dbprintf("\nNumber of Reps: %u",overflowReps);
    // Setup timer and interrupt
    OpenTimer3(T3_ON | T3_SOURCE_INT | T3_PS_1_8, overflowPeriod);
//    OpenTimer5(T5_ON | T5_IDLE_STOP | T5_GATE_OFF | T5_PS_1_8 | T5_SOURCE_INT,overflowPeriod);
//    OpenTimer5(T5_ON | T5_PS_1_8 | T5_SOURCE_INT, overflowPeriod);
    ConfigIntTimer3(T3_INT_ON | T3_INT_PRIOR_3 );
    mT3IntEnable(1);
    stepperState = inited;
    return SUCCESS;
}

char Stepper_ChangeStepRate(unsigned short int rate)
{
    unsigned short int overflowPeriod;
    if ((rate > TWENTY_KILOHERTZ)||(stepperState == off)) return ERROR;
    dbprintf("\nChanging step rate");
    T5CONbits.ON = 0; // halt timer5
    overflowPeriod = CalculateOverflowPeriod(rate);
    WritePeriod5(overflowPeriod);
    if (stepperState != halted) {
        T3CONbits.ON = 1; // restart timer3
    }
    return SUCCESS;
}

char Stepper_SetSteps(char direction, unsigned int steps)
{
    if (stepperState == off) return ERROR;
    if ((direction==FORWARD)||(direction==REVERSE)) {
        stepDir = direction;
        stepCount = steps;
        switch(stepperState) {
            case waiting:
            case inited:
                stepperState = STEPPER_MODE;
                break;
            default:
                break;
        }
        return SUCCESS;
    }
    return ERROR;
}
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

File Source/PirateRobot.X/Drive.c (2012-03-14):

/*
 * File:   Drive.c
 * Author: dagoodma jurjohns
 *
 * Created on March 2, 2012
 */
//#define DRIVE_TEST

#include <p32xxxx.h>
#include "serial.h"
#include "PORTS.h"
#include "pwm.h"
#include "Drive.h"
#include "AD.h"
#include "LED.h"
#include "Util.h"

/*******************************************************************************
 * PRIVATE #DEFINES                                                            *
 ******************************************************************************/
#define USE_BATPWM
#define DEBUG_VERBOSE
#ifdef DEBUG_VERBOSE
    #define dbprintf(...) printf(__VA_ARGS__)
#else
    #define dbprintf(...)
#endif

#define MOTOR_A_PWM PWM_PORTY10
#define MOTOR_A_DIR PORTY09_LAT
#define MOTOR_A_DIR_TRIS PORTY09_TRIS
#define MOTOR_B_PWM PWM_PORTY12
#define MOTOR_B_DIR PORTY11_LAT
#define MOTOR_B_DIR_TRIS PORTY11_TRIS

#define LEFT 0
#define RIGHT 1
#define FREQUENCY_PWM 250
#define BAT_MAX 305 // (1023 * Vbat) / (10 * 3.3) => Vbat = 9.8 V
#define UPDATE_DELAY 100
#define TIMER_NUM 5


/*******************************************************************************
 * PRIVATE VARIABLES                                                           *
 ******************************************************************************/
enum motor {B, A};
enum direction {FORWARD, REVERSE};

static unsigned char motorPWM[] = {MOTOR_A_PWM, MOTOR_B_PWM};
static unsigned int motorPWMValue[] = {0, 0};
static unsigned char motorSpeed[] = { 0, 0 };

/*******************************************************************************
 * PRIVATE FUNCTIONS PROTOTYPES                                                *
 ******************************************************************************/
static void SetDirection(int motor, int direction);

/*************************************

******************************************
 * PRIVATE FUNCTIONS                                                           *
 ******************************************************************************/
static void SetDirection(int motor, int direction) {

    if (motor == A) {
        MOTOR_A_DIR = !direction;
    }
    else {
        MOTOR_B_DIR = !direction;
    }
}

static char SetSpeed(int motor, char speed) {
    // TODO add error checking
    motorSpeed[motor] =  speed;
    //printf("\nPWM should be = %f", speed * 80.0);
 
    unsigned int pwm = 0;
    if (speed > 0) {
#ifdef USE_BATPWM
        int battery = (float)ReadADPin(BAT_VOLTAGE);
#else
        int battery = 0;
#endif
        float pwm_modifier = 100.0 * ((1.0 - 1.0*(battery/BAT_MAX)) * 2.15);
        //printf("\nMultiplier =%f", max((int)pwm_modifier, 0));
        pwm = (unsigned int)(speed * 90.0 + max((int)pwm_modifier, 0));
    }
    motorPWMValue[motor] = pwm;
    //printf("\nPWM is=%i", pwm);
    pwm = min(pwm, 1000);
    pwm = max(pwm, 0);

    SetDutyCycle(motorPWM[motor], pwm);
}

void SetMotor(int motor, int direction, char speed) {
    SetDirection(motor, direction);
    SetSpeed(motor, speed);
}


/*******************************************************************************
 * PUBLIC FUNCTIONS                                                           *
 ******************************************************************************/

char Drive_Init(void) {
    // Set motor direction outputs
    MOTOR_A_DIR_TRIS = 0;
    MOTOR_B_DIR_TRIS = 0;

    PWM_Init(MOTOR_A_PWM |  MOTOR_B_PWM, FREQUENCY_PWM);
    Drive_Stop();
    InitTimer(TIMER_NUM,UPDATE_DELAY);

    return SUCCESS;
}

char Drive_Update(void) {
    /*
    if (IsTimerExpired(TIMER_NUM)) {
        SetSpeed(A, motorSpeed[A]);
        SetSpeed(B, motorSpeed[B]);
        InitTimer(TIMER_NUM, UPDATE_DELAY);
    }
     */
    return SUCCESS;
}
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

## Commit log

2012-02-22 Initial commit, checkoff 2 done
    [PitcherRelease.SLDASM, genevaWheel.SLDPRT, pingPongBall.SLDPRT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]
2012-02-24 One day til checkoff 3
    [12V65RPMGearheadMotor.SLDPRT, BotBody.SLDPRT, BoxBottom.SLDPRT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]
2012-02-28 Ready for checkoff 4
    [ACTUATORS.DSN, BotBody.SLDPRT, BoxBottom.SLDPRT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]
2012-03-04 Test tape sensors, writing bumper sensors
    [Bumper.SLDASM, Bumper.SLDDRW, Bumper_short.SLDASM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]
2012-03-05 Finished IR code, updated tape test harness
    [Uno32_IO_board.xlsx, wheelMDF2.SLDPRT]
2012-03-12 Sunday, runs half of course.
    [Bumper.SLDASM, Bumper_short.SLDASM, Platform.SLDASM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]
2012-03-14 Ready for minspec.
    [SENSORS.DSN, Uno32_IO_board.xlsx, motorMountFront1 (Hugo Hernandez's conflicted copy 2012-02-22).SLDPRT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]
2012-03-20 Project finished. Turned in report.
    [ACTUATORS.DSN, Bumper.SLDASM, Bumper_short.SLDASM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]
